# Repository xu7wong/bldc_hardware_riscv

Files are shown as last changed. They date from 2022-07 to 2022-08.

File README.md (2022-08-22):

# bldc_hardware_riscv

Ki-Cad 6.99 project
Windows version download:

https://mirrors.tuna.tsinghua.edu.cn/kicad/windows/nightly/

Teardrop config file:

https://forum.kicad.info/t/kicad6-99-finally-added-the-teardrop-feature-non-plugins/33192

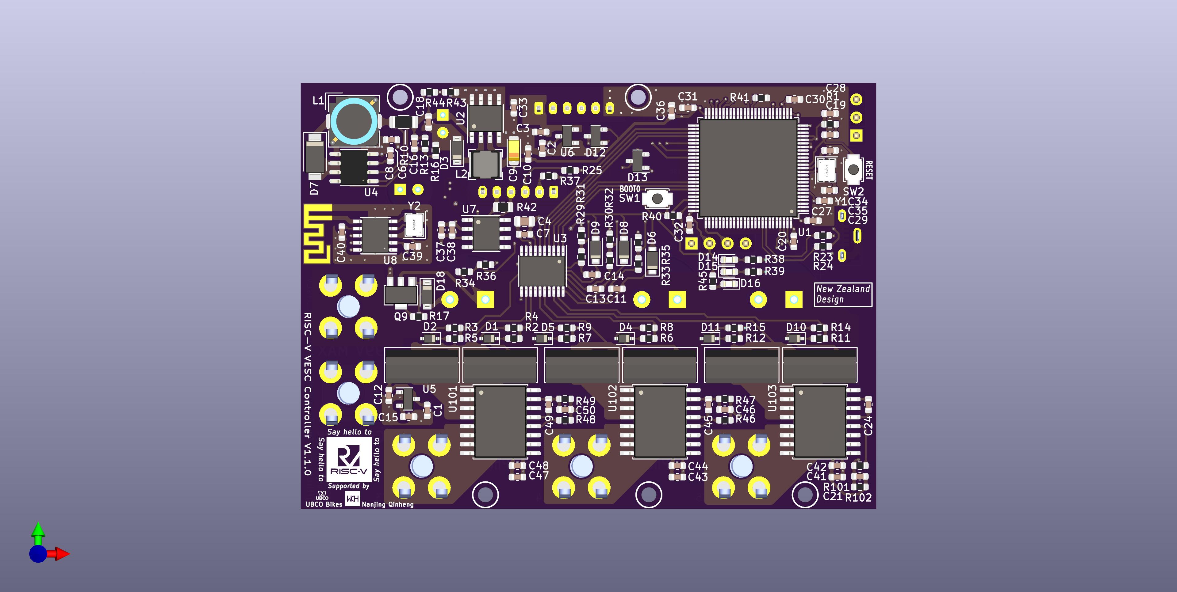
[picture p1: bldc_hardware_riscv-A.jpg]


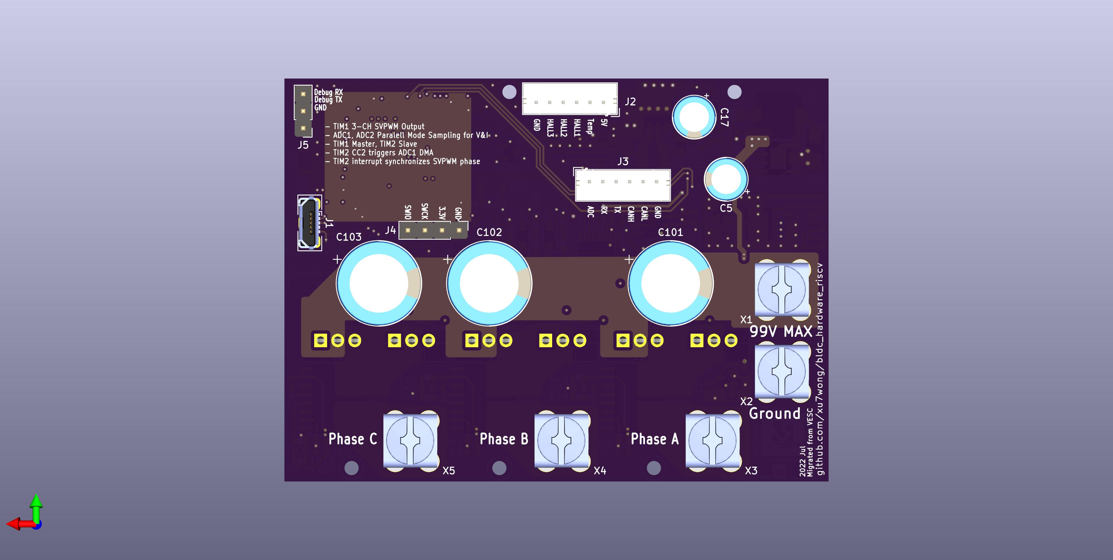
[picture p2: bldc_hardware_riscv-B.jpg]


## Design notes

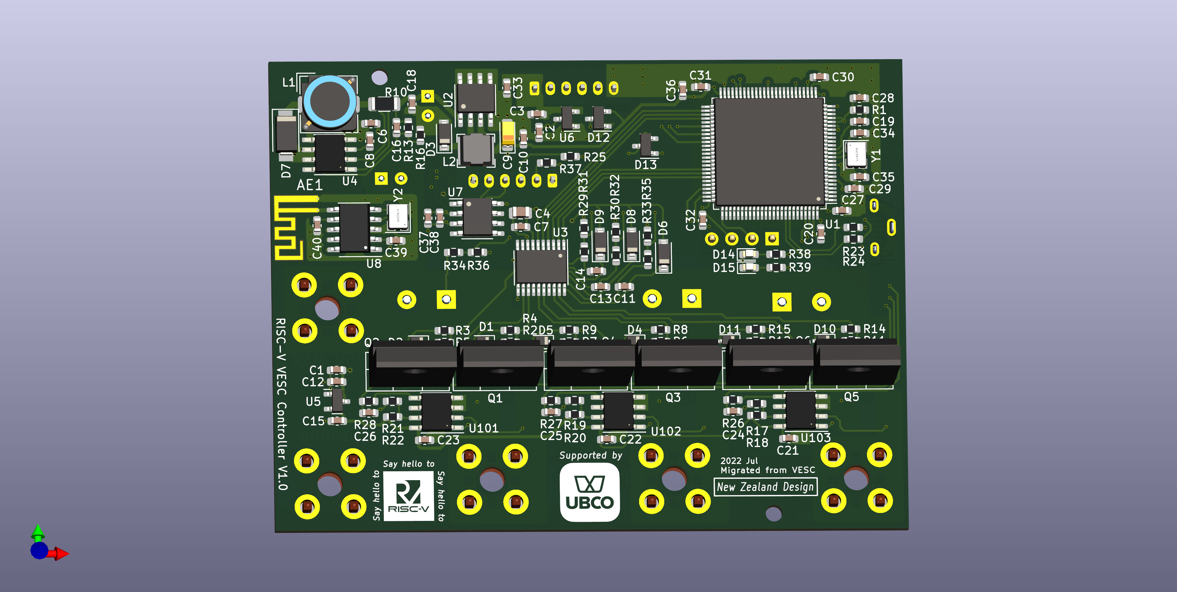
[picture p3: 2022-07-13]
bldc_hardware_riscv/bldc_hardware_riscv.png

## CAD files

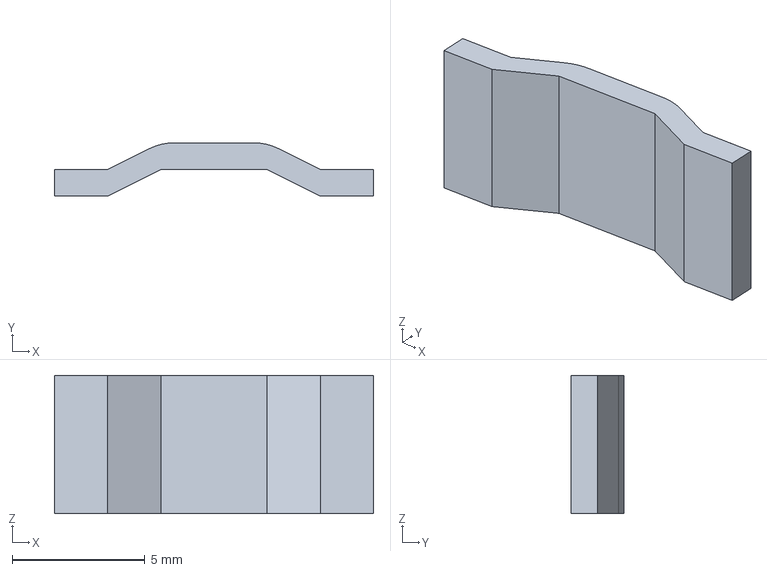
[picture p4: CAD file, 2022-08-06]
bldc_hardware_riscv/3D/3920.stp
12.0 x 2.00 x 5.20 mm

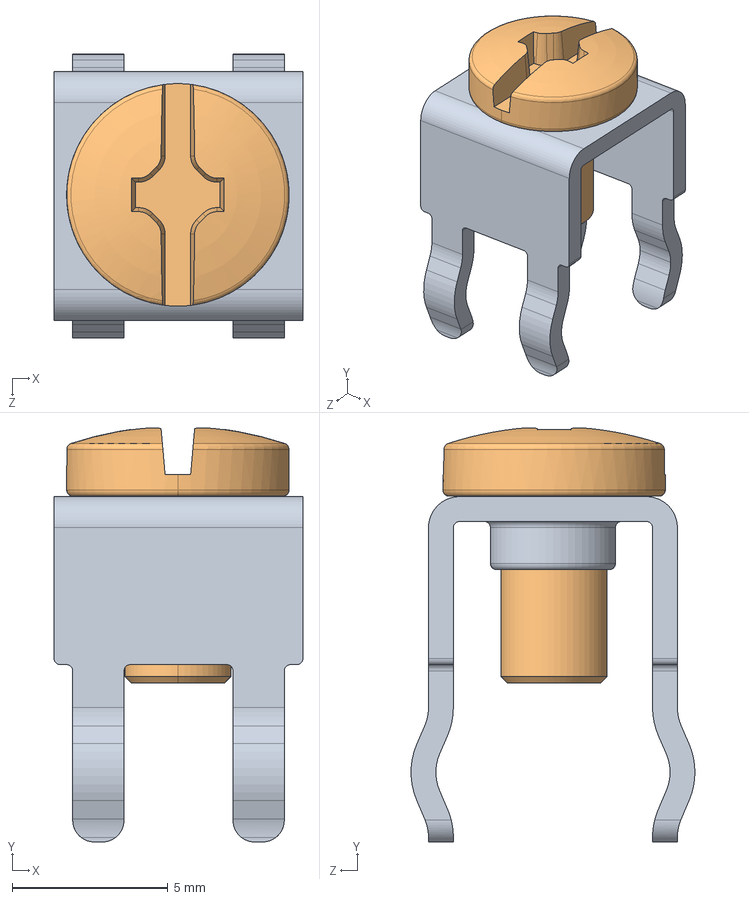
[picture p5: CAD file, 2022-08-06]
bldc_hardware_riscv/3D/User Library-Keystone_7693.STEP
8.00 x 13.3 x 9.12 mm
Keystone_7691
6-32-panhead_6mm_thd

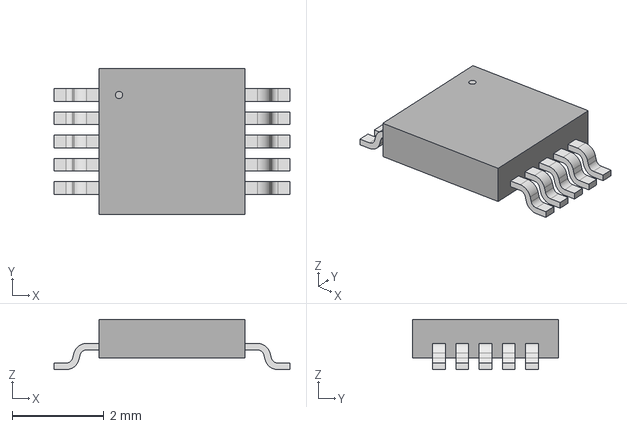
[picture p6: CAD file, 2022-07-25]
bldc_hardware_riscv/3D/TSSOP10_3X3_MCH.step
5.16 x 3.20 x 1.09 mm

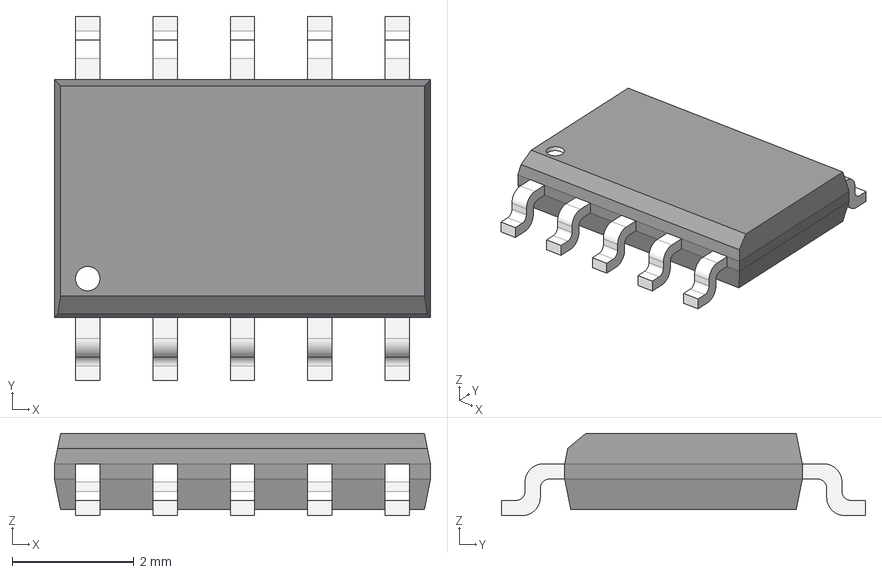
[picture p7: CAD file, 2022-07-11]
bldc_hardware_riscv/3D/SO10 Narrow 3.9mm.step
6.17 x 5.98 x 1.35 mm

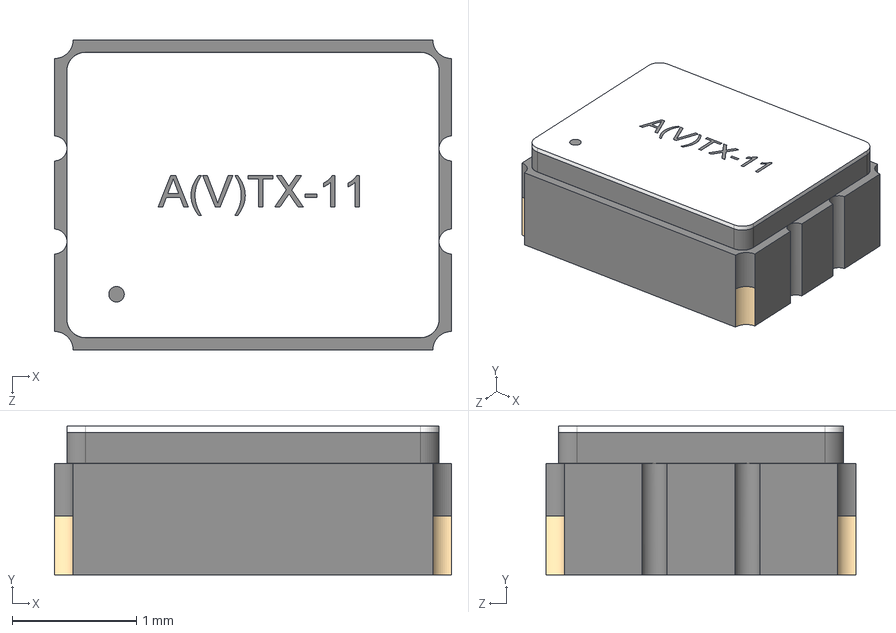
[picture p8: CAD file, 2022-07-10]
bldc_hardware_riscv/3D/ATX-11.STEP
3.20 x 1.20 x 2.50 mm

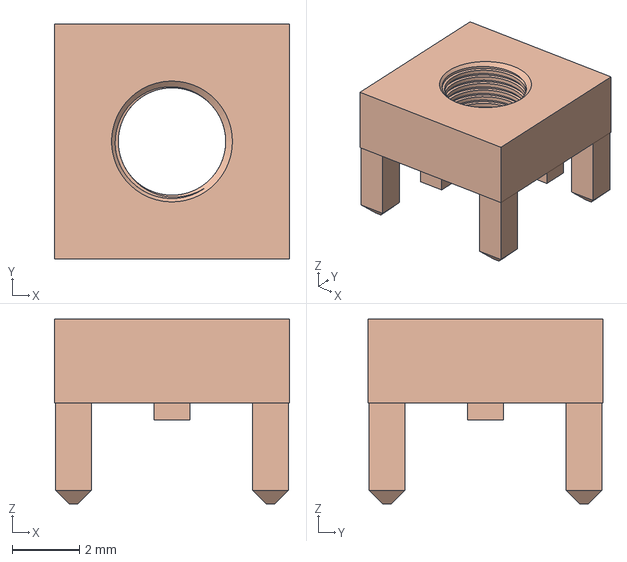
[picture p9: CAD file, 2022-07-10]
bldc_hardware_riscv/3D/74650073 (rev1).stp
7.00 x 7.00 x 5.50 mm

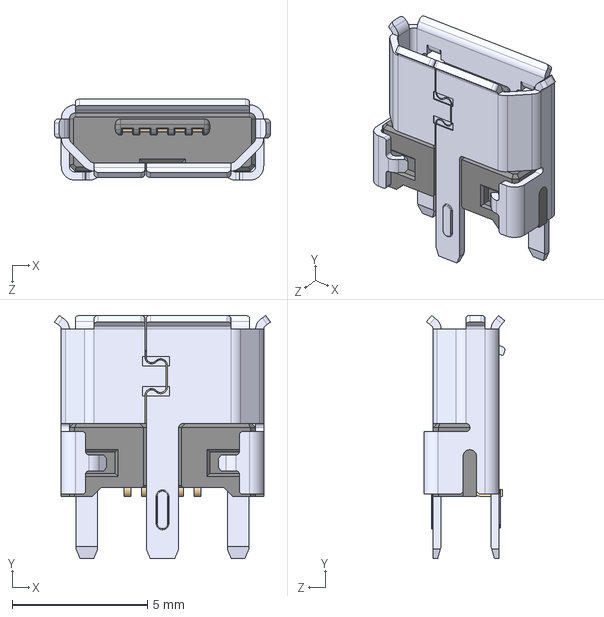
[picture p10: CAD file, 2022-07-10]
bldc_hardware_riscv/3D/105133-0001--3DModel-STEP-1.STEP
8.00 x 9.00 x 3.01 mm

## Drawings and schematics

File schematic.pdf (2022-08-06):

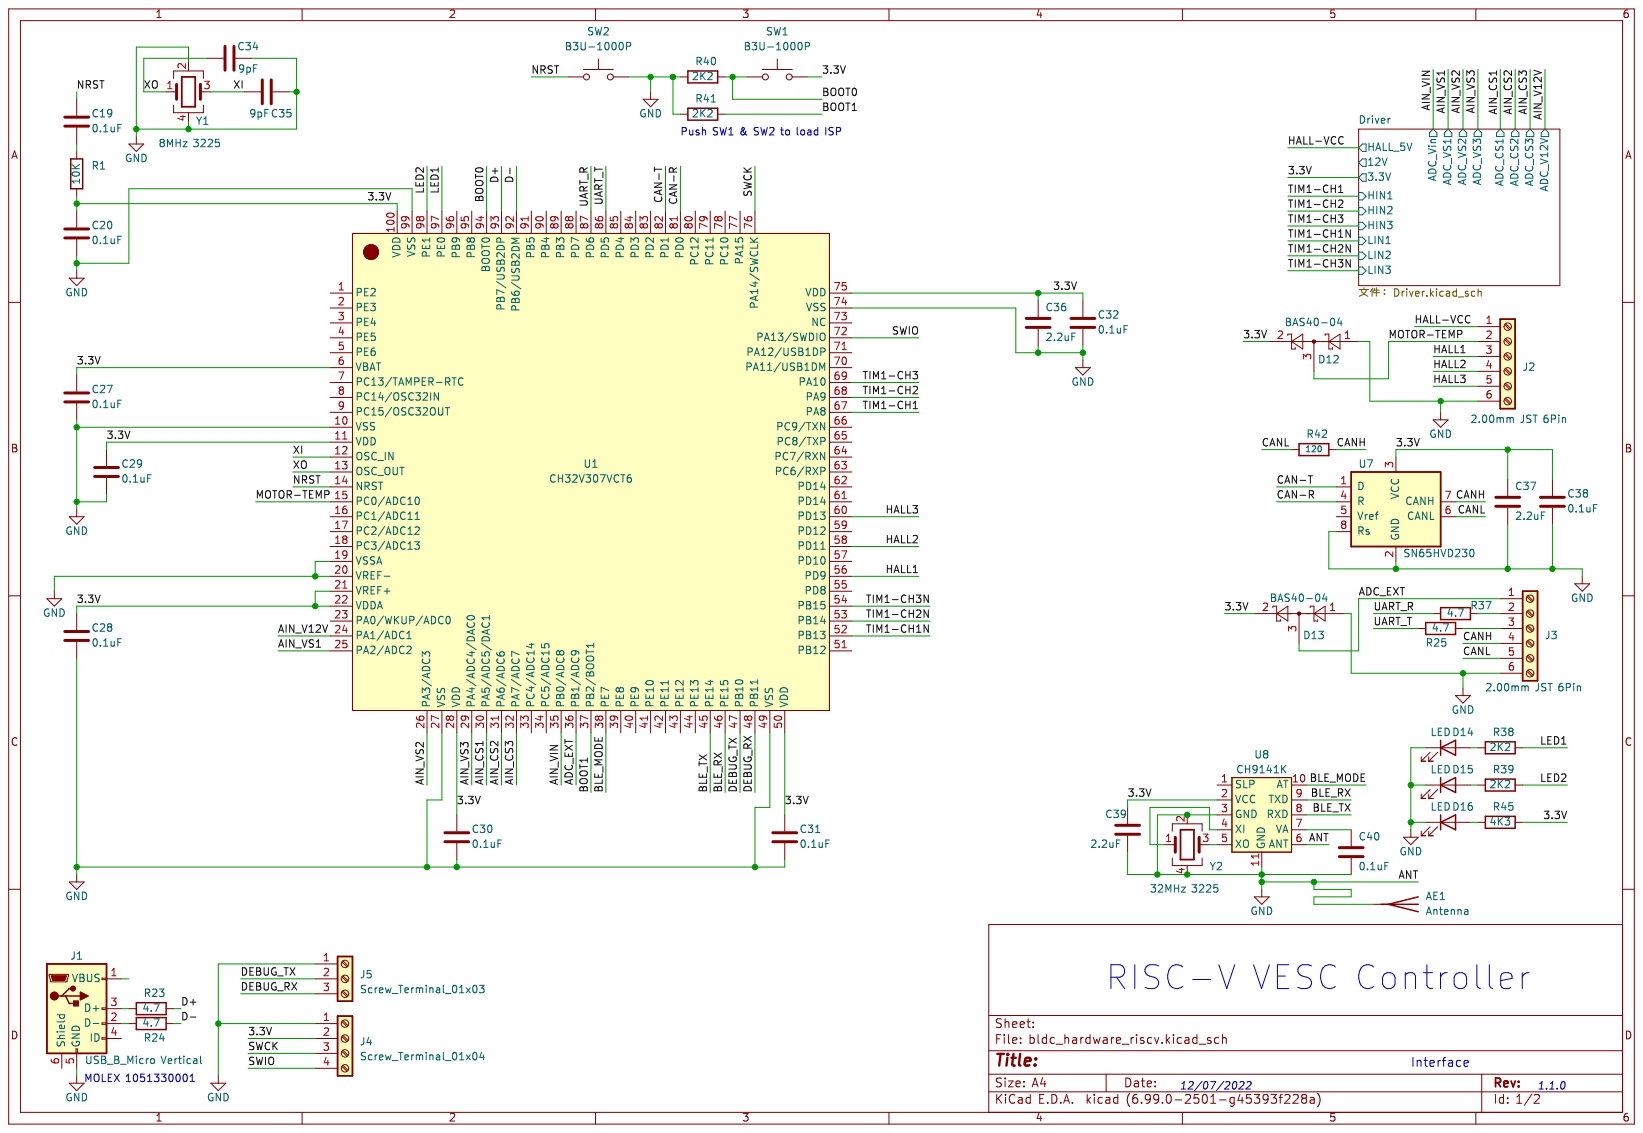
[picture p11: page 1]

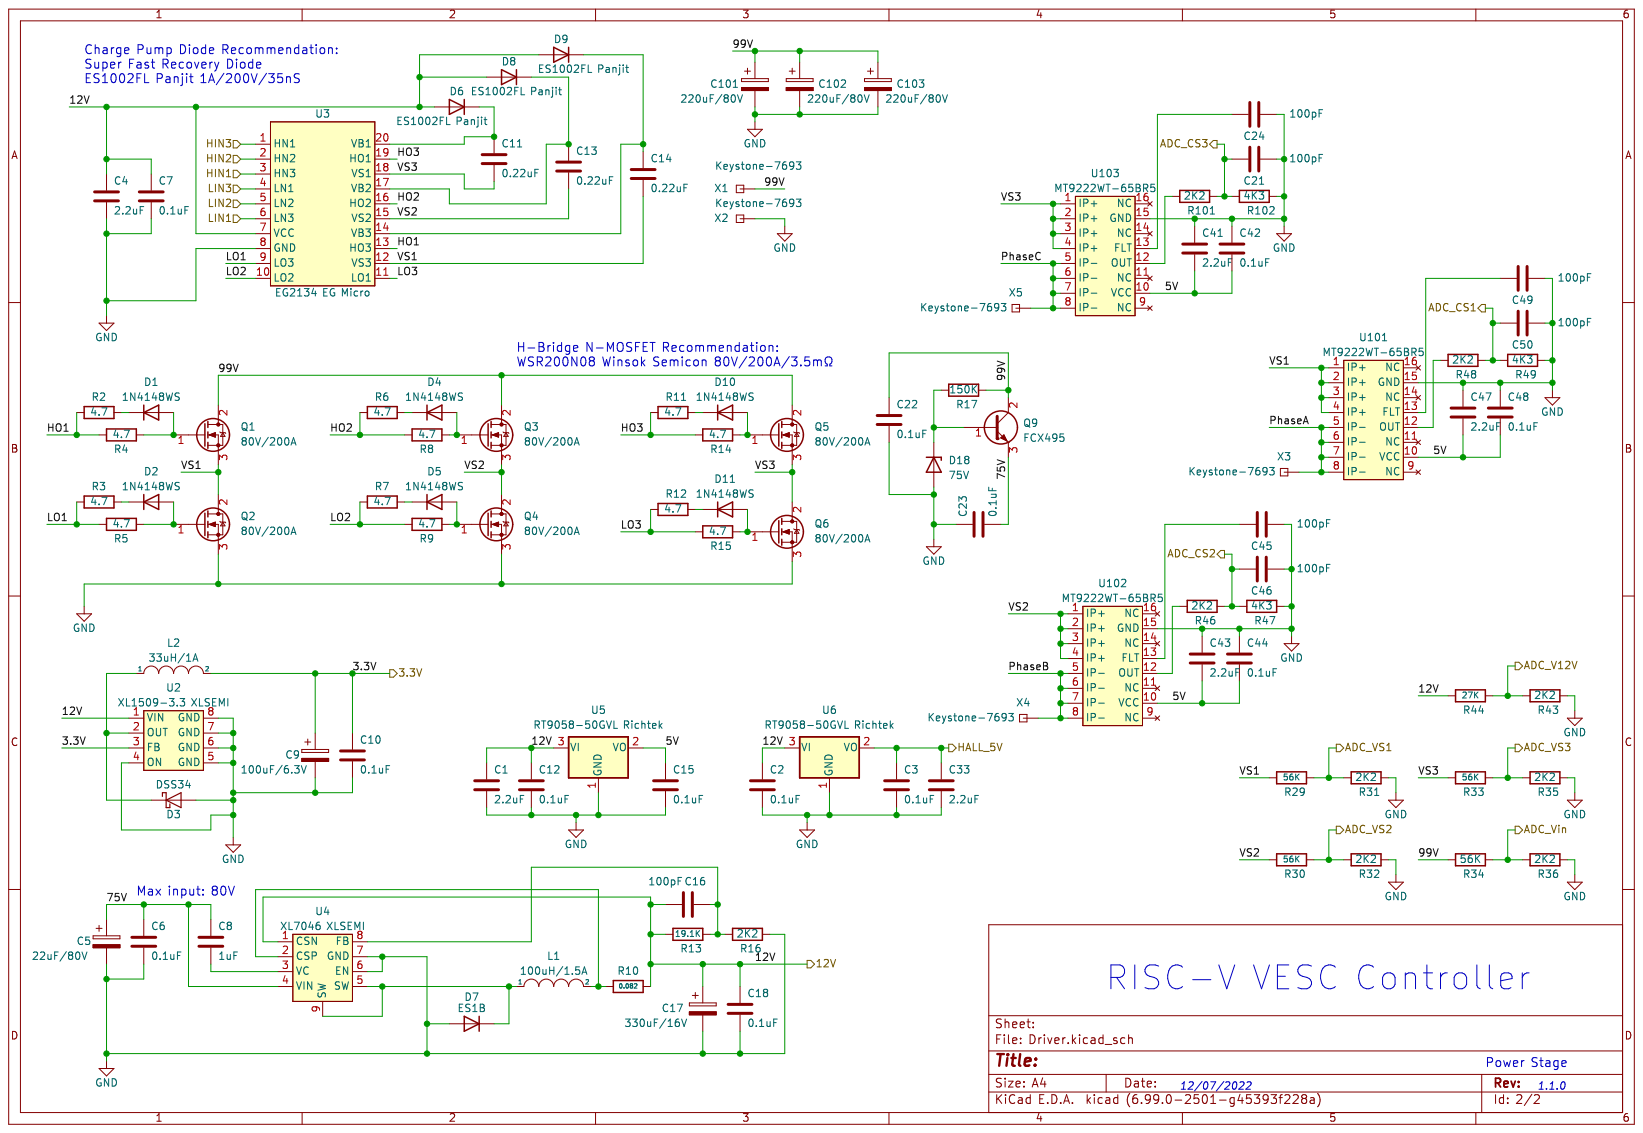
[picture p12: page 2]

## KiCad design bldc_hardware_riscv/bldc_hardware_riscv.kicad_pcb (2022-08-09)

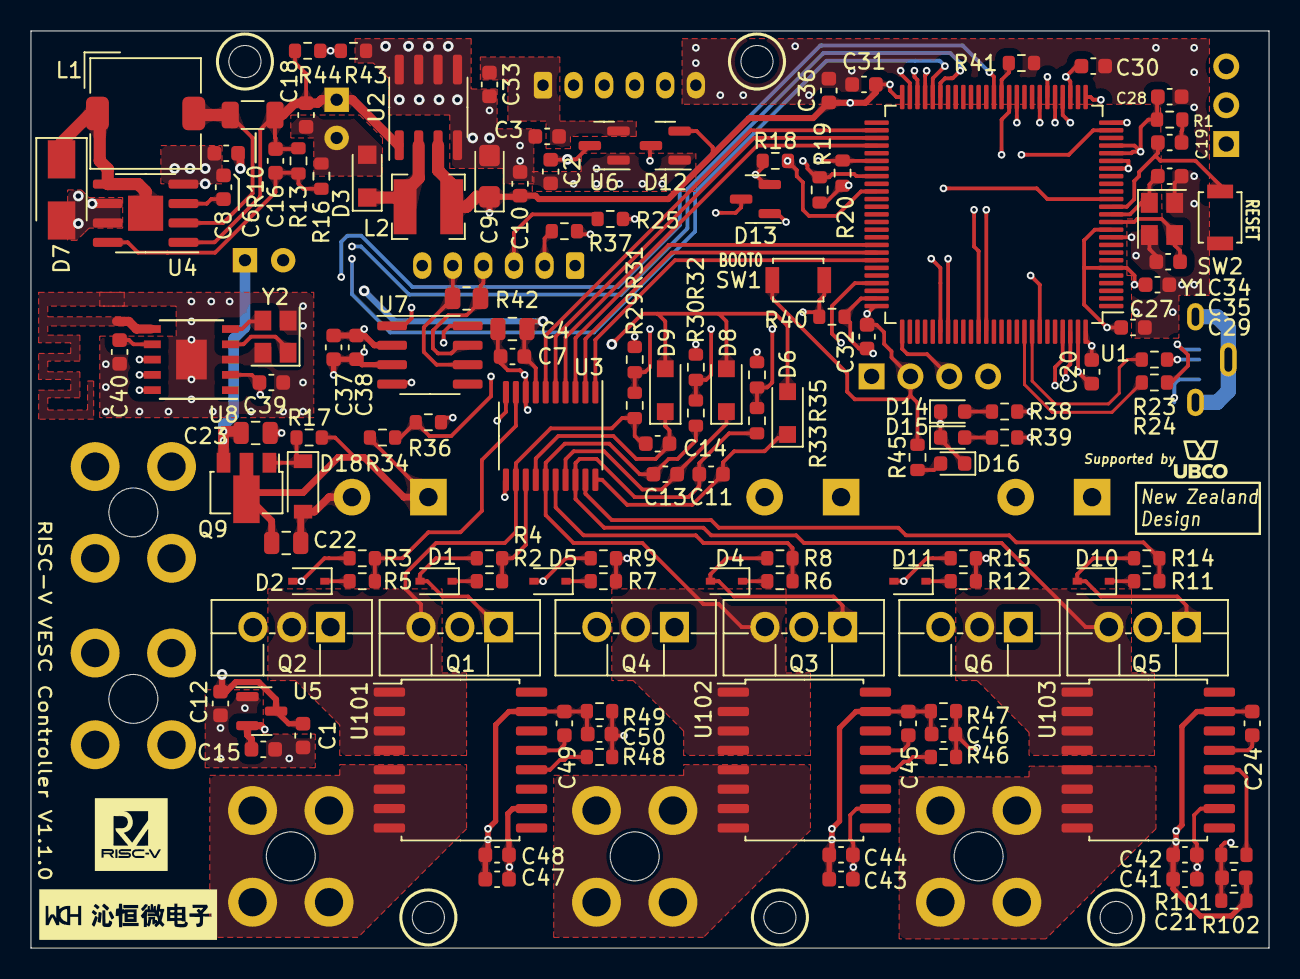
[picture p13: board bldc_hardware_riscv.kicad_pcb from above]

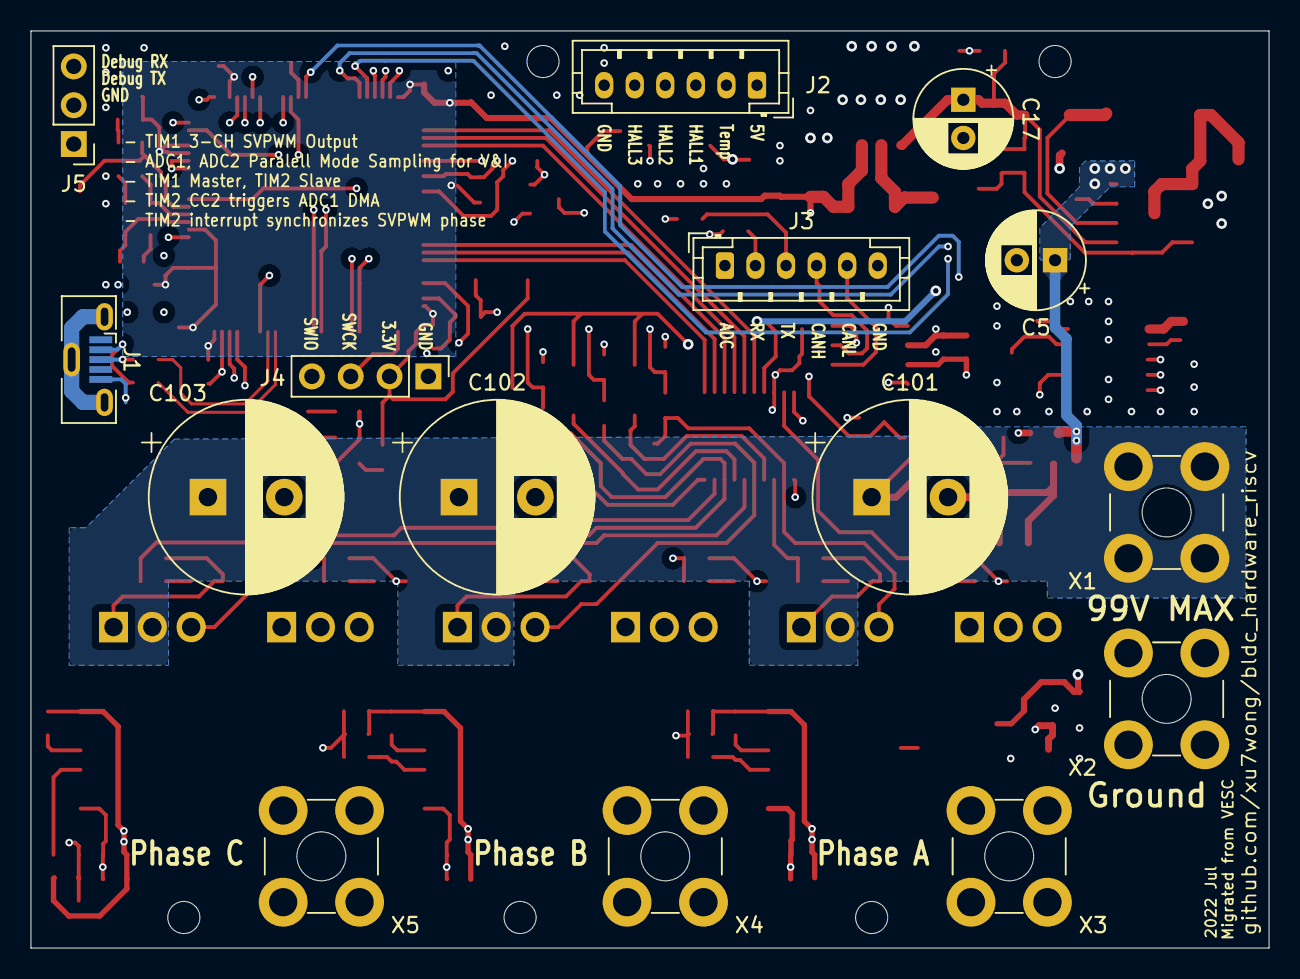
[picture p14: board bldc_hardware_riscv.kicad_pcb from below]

Board: 4 copper layers, 81.0 x 60.0 mm, 148 parts (15 on the bottom side), 98 nets.

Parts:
C1, C33, C36, C37, C39, C41, C43, C47: 2.2uF; C_0603_1608Metric
C2, C3, C6, C7, C10, C12, C15, C18, C19, C20, C27, C28, C29, C30, C31, C32, C38, C40, C42, C44, C48: 0.1uF; C_0603_1608Metric
C4: 2.2uF; C_0805_2012Metric
C5: 22uF/80V; CP_Radial_D6.3mm_P2.50mm
C8: 1uF; C_0603_1608Metric
C9: 100uF/6.3V; CP_EIA-3216-18_Kemet-A
C11, C13, C14: 0.22uF; C_0603_1608Metric
C16, C21, C24, C45, C46, C49, C50: 100pF; C_0603_1608Metric
C17: 330uF/16V; CP_Radial_D6.3mm_P2.50mm
C22, C23: 0.1uF; C_0805_2012Metric
C34, C35: 9pF; C_0603_1608Metric
C101, C102, C103: 220uF/80V; CP_Radial_D12.5mm_P5.00mm
D1, D2, D4, D5, D10, D11: 1N4148WS; D_SOD-323
D3: DSS34; Nexperia_CFP3_SOD-123W
D6, D8, D9: ES1002FL Panjit; D_SOD-123F
D7: ES1B; D_SMA
D12, D13: BAS40-04; SOT-23
D14, D15, D16: LED; LED_0603_1608Metric
D18: 75V; D_SOD-123
J1: USB_B_Micro Vertical; USB_Micro-B_Molex-105133-0001
J2, J3: 2.00mm JST 6Pin; JST_PH_B6B-PH-K_1x06_P2.00mm_Vertical
J4: Screw_Terminal_01x04; PinHeader_1x04_P2.54mm_Vertical
J5: Screw_Terminal_01x03; PinHeader_1x03_P2.54mm_Vertical
L1: 100uH/1.5A; L_TDK_SLF7032
L2: 33uH/1A; L_Bourns-SRN4018
Q1, Q2, Q3, Q4, Q5, Q6: 80V/200A; TO-220F-3_Vertical
Q9: FCX495; SOT-89-3
R1: 10K; R_0603_1608Metric
R2, R3, R4, R5, R6, R7, R8, R9, R11, R12, R14, R15, R23, R24, R25, R37: 4.7; R_0603_1608Metric
R10: 0.082; R_1206_3216Metric
R13: 19.1K; R_0603_1608Metric
R16, R18, R19, R20, R31, R32, R35, R36, R38, R39, R40, R41, R43, R46, R48, R101: 2K2; R_0603_1608Metric
R17: 150K; R_0603_1608Metric
R29, R30, R33, R34: 56K; R_0603_1608Metric
R42: 120; R_0805_2012Metric
R44: 27K; R_0603_1608Metric
R45, R47, R49, R102: 4K3; R_0603_1608Metric
SW1, SW2: B3U-1000P; SW_SPST_B3U-1000P
U1: CH32V307VCT6; LQFP-100_14x14mm_P0.5mm
U2: XL1509-3.3 XLSEMI; SOIC-8_3.9x4.9mm_P1.27mm
U3: EG2134 EG Micro; TSSOP-20_4.4x6.5mm_P0.65mm
U4: XL7046 XLSEMI; HSOP-8-1EP_3.9x4.9mm_P1.27mm_EP2.3x2.3mm
U5, U6: RT9058-50GVL Richtek; SOT-23
U7: SN65HVD230; SOIC-8_3.9x4.9mm_P1.27mm
U8: CH9141K; SSOP-10_3.9x4.9mm_P1.00mm
U101, U102, U103: MT9222WT-65BR5; SOIC-16W_7.5x10.3mm_P1.27mm
X1, X2, X3, X4, X5: Keystone-7693
Y1: 8MHz 3225; Oscillator_SMD_Abracon_ASE-4Pin_3.2x2.5mm
Y2: 32MHz 3225; Oscillator_SMD_Abracon_ASE-4Pin_3.2x2.5mm

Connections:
/3.3V: C9.1, C10.1, C20.1, C27.1, C28.1, C29.1, C30.1, C31.1, C32.1, C36.1, C37.1, C38.1, C39.1, D12.2, D13.2, J4.2, L2.2, R1.2, R18.2, R19.2, R20.2, R45.2, SW1.2, U1.6 (VBAT), U1.11 (VDD), U1.21 (VREF+), U1.22 (VDDA), U1.28 (VDD), U1.50 (VDD), U1.75 (VDD), U1.100 (VDD), U2.3 (FB), U7.3 (VCC), U8.2 (VCC)
/ADC_EXT: D13.3, J3.1, U1.36 (PB1/ADC9)
/AIN_CS1: C50.1, R48.2, R49.1, U1.30 (PA5/ADC5/DAC1)
/AIN_CS2: C46.1, R46.2, R47.1, U1.31 (PA6/ADC6)
/AIN_CS3: C21.1, R101.2, R102.1, U1.32 (PA7/ADC7)
/AIN_V12V: R43.1, R44.2, U1.24 (PA1/ADC1)
/AIN_VIN: R34.2, R36.1, U1.35 (PB0/ADC8)
/AIN_VS1: R29.2, R31.1, U1.25 (PA2/ADC2)
/AIN_VS2: R30.2, R32.1, U1.26 (PA3/ADC3)
/AIN_VS3: R33.2, R35.1, U1.29 (PA4/ADC4/DAC0)
/BLE_MODE: U1.38 (PE7), U8.10 (AT)
/BLE_RX: U1.46 (PE15), U8.9 (TXD)
/BLE_TX: U1.45 (PE14), U8.8 (RXD)
/BOOT0: R40.1, SW1.1, U1.94 (BOOT0)
/BOOT1: R41.1, U1.37 (PB2/BOOT1)
/CAN-R: U1.81 (PD0), U7.4 (R)
/CAN-T: U1.82 (PD1), U7.1 (D)
/CANH: J3.4, R42.2, U7.7 (CANH)
/CANL: J3.5, R42.1, U7.6 (CANL)
/D+: R23.2, U1.93 (PB7/USB2DP)
/D-: R24.2, U1.92 (PB6/USB2DM)
/DEBUG_RX: J5.3, U1.48 (PB11)
/DEBUG_TX: J5.2, U1.47 (PB10)
/Driver/5V: C15.1, C41.2, C42.2, C43.2, C44.2, C47.2, C48.2, U5.2 (VO), U101.10 (VCC), U102.10 (VCC), U103.10 (VCC)
/Driver/12V: C1.1, C2.1, C4.1, C7.1, C12.1, C16.1, C17.1, C18.1, D6.2 (A), D8.2 (A), D9.2 (A), R10.2, R13.1, R44.1, U2.1 (VIN), U3.7 (VCC), U4.1 (CSN), U5.3 (VI), U6.3 (VI)
/Driver/75V: C5.1, C6.1, C8.1, C23.2, Q9.3 (E), U4.4 (VIN)
/Driver/99V: C22.1, C101.1, C102.1, C103.1, Q1.2 (D), Q3.2 (D), Q5.2 (D), Q9.2 (C), R17.2, R34.1, X1.1
/Driver/HO1: R2.1, R4.1, U3.13 (HO3)
/Driver/HO2: R6.1, R8.1, U3.16 (HO2)
/Driver/HO3: R11.1, R14.1, U3.19 (HO1)
/Driver/LO1: R3.1, R5.1, U3.9 (LO3)
/Driver/LO2: R7.1, R9.1, U3.10 (LO2)
/Driver/LO3: R12.1, R15.1, U3.11 (LO1)
/Driver/PhaseA: U101.5 (IP-), U101.6 (IP-), U101.7 (IP-), U101.8 (IP-), X3.1
/Driver/PhaseB: U102.5 (IP-), U102.6 (IP-), U102.7 (IP-), U102.8 (IP-), X4.1
/Driver/PhaseC: U103.5 (IP-), U103.6 (IP-), U103.7 (IP-), U103.8 (IP-), X5.1
/Driver/VS1: C14.2, Q1.3 (S), Q2.2 (D), R29.1, U3.12 (VS3), U101.1 (IP+), U101.2 (IP+), U101.3 (IP+), U101.4 (IP+)
/Driver/VS2: C13.2, Q3.3 (S), Q4.2 (D), R30.1, U3.15 (VS2), U102.1 (IP+), U102.2 (IP+), U102.3 (IP+), U102.4 (IP+)
/Driver/VS3: C11.2, Q5.3 (S), Q6.2 (D), R33.1, U3.18 (VS1), U103.1 (IP+), U103.2 (IP+), U103.3 (IP+), U103.4 (IP+)
/HALL1: J2.3, R20.1, U1.56 (PD9)
/HALL2: J2.4, R19.1, U1.58 (PD11)
/HALL3: J2.5, R18.1, U1.60 (PD13)
/HALL-VCC: C3.1, C33.1, J2.1, U6.2 (VO)
/LED1: R38.2, U1.97 (PE0)
/LED2: R39.2, U1.98 (PE1)
/MOTOR-TEMP: D12.3, J2.2, U1.15 (PC0/ADC10)
/NRST: C19.2, SW2.1, U1.14 (NRST)
/SWCK: J4.3, U1.76 (PA14/SWCLK)
/SWIO: J4.4, U1.72 (PA13/SWDIO)
/TIM1-CH1: U1.67 (PA8), U3.3 (HN3)
/TIM1-CH1N: U1.52 (PB13), U3.6 (LN3)
/TIM1-CH2: U1.68 (PA9), U3.2 (HN2)
/TIM1-CH2N: U1.53 (PB14), U3.5 (LN2)
/TIM1-CH3: U1.69 (PA10), U3.1 (HN1)
/TIM1-CH3N: U1.54 (PB15), U3.4 (LN1)
/UART_R: R37.1, U1.87 (PD6)
/UART_T: R25.1, U1.86 (PD5)
/XI: C35.1, U1.12 (OSC_IN), Y1.3
/XO: C34.1, U1.13 (OSC_OUT), Y1.1
GND: C1.2, C2.2, C3.2, C4.2, C5.2, C6.2, C7.2, C9.2, C10.2, C12.2, C15.2, C17.2, C18.2, C20.2, C21.2, C22.2, C23.1, C24.2, C27.2, C28.2, C29.2, C30.2, C31.2, C32.2, C33.2, C34.2, C35.2, C36.2, C37.2, C38.2, C39.2, C40.2, C41.1, C42.1, C43.1, C44.1, C45.2, C46.2, C47.1, C48.1, C49.2, C50.2, C101.2, C102.2, C103.2, D3.2 (A), D7.2 (A), D12.1, D13.1, D14.1 (K), D15.1 (K), D16.1 (K), D18.2 (A), J1.5 (GND), J2.6, J3.6, J4.1, J5.1, Q2.3 (S), Q4.3 (S), Q6.3 (S), R16.2, R31.2, R32.2, R35.2, R36.2, R40.2, R41.2, R43.2, R47.2, R49.2, R102.2, SW2.2, U1.10 (VSS), U1.19 (VSSA), U1.20 (VREF-), U1.27 (VSS), U1.49 (VSS), U1.74 (VSS), U1.99 (VSS), U2.4 (ON), U2.5 (GND), U2.6 (GND), U2.7 (GND), U2.8 (GND), U3.8 (GND), U4.6 (EN), U4.7 (GND), U5.1 (GND), U6.1 (GND), U7.2 (GND), U7.8 (Rs), U8.3 (GND), U8.6 (ANT), U8.11 (GND), U101.15 (GND), U102.15 (GND), U103.15 (GND), X2.1, Y1.2, Y1.4, Y2.2, Y2.4
unnamed: C19.1, R1.1
unnamed: D1.2 (A), Q1.1 (G), R4.2
unnamed: D1.1 (K), R2.2
unnamed: D2.2 (A), Q2.1 (G), R5.2
unnamed: D2.1 (K), R3.2
unnamed: D3.1 (K), L2.1, U2.2 (OUT)
unnamed: D4.2 (A), Q3.1 (G), R8.2
unnamed: D4.1 (K), R6.2
unnamed: D5.2 (A), Q4.1 (G), R9.2
unnamed: D5.1 (K), R7.2
unnamed: C11.1, D6.1 (K), U3.20 (VB1)
unnamed: D7.1 (K), L1.1, U4.5 (SW), U4.9 (SW)
unnamed: C13.1, D8.1 (K), U3.17 (VB2)
unnamed: C14.1, D9.1 (K), U3.14 (VB3)
unnamed: D10.2 (A), Q5.1 (G), R14.2
unnamed: D10.1 (K), R11.2
unnamed: D11.2 (A), Q6.1 (G), R15.2
unnamed: D11.1 (K), R12.2
unnamed: D14.2 (A), R38.1
unnamed: D15.2 (A), R39.1
unnamed: D16.2 (A), R45.1
unnamed: D18.1 (K), Q9.1 (B), R17.1
unnamed: J1.3 (D+), R23.1
unnamed: J1.2 (D-), R24.1
unnamed: J3.2, R37.2
unnamed: J3.3, R25.2
unnamed: L1.2, R10.1, U4.2 (CSP)
unnamed: C16.2, R13.2, R16.1, U4.8 (FB)
unnamed: C8.2, U4.3 (VC)
unnamed: C40.1, U8.7 (VA)
unnamed: U8.4 (XI), Y2.1
unnamed: U8.5 (XO), Y2.3
unnamed: C49.1, U101.13 (FLT)
unnamed: R48.1, U101.12 (OUT)
unnamed: C45.1, U102.13 (FLT)
unnamed: R46.1, U102.12 (OUT)
unnamed: C24.1, U103.13 (FLT)
unnamed: R101.1, U103.12 (OUT)

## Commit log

2022-07-10 add sch & pcb
    [105133-0001--3DModel-STEP-1.STEP, 74650073 (rev1).stp, ATX-11.STEP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]
2022-07-11 First release to PCB manufacture
    [Driver.kicad_sch, SO10 Narrow 3.9mm.step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]
2022-07-11 add 2 pages schematic
2022-07-13 fix resistor/inductor/capacitor parameters, add boot button, add 120Ohm CAN bus load resistor.
    [Driver.kicad_sch, bldc_hardware_riscv.kicad_pcb, bldc_hardware_riscv.kicad_sch]
2022-07-19 update gbr with teardrop
    [bldc_hardware_riscv-B_Cu.gbr, bldc_hardware_riscv-B_Mask.gbr, bldc_hardware_riscv-B_Silkscreen.gbr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]
2022-07-19 add teardrop by Kicad V6.99
    [bldc_hardware_riscv.kicad_pcb]
2022-07-19 update SCH by Kicad V6.99
    [Driver.kicad_sch, bldc_hardware_riscv.kicad_sch]
2022-07-19 add html BOM
2022-07-24 add debug RX/TX, fix CH9141K footprint error, add 12V detection
    [Driver.kicad_sch, bldc_hardware_riscv.kicad_pcb, bldc_hardware_riscv.kicad_sch]
2022-07-25 fix PCB DRC error, fix CH9141K 3D preview
    [TSSOP10_3X3_MCH.step, bldc_hardware_riscv.kicad_pcb]
2022-08-06 use hall current sensor (60A limit), use keystone terminal, support up to 120V input
    [3920.stp, Driver.kicad_sch, User Library-Keystone_7693.STEP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]
2022-08-06 add missed caps
    [Driver.kicad_sch, bldc_hardware_riscv.kicad_pcb, bldc_hardware_riscv.kicad_sch]
2022-08-09 Update WCH LOGO, fixed gbr clearance issue (around MCU range)
    [bldc_hardware_riscv-B_Cu.gbr, bldc_hardware_riscv-B_Mask.gbr, bldc_hardware_riscv-B_Silkscreen.gbr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]
